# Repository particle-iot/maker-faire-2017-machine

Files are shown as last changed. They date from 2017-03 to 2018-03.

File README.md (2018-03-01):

# Maker Faire Machine

Welcome friends! Put all the amazing code, diagrams, PCB files and other
artifacts needed to build the Machine here.

# License

Copyright (C) 2017 Particle Industries Inc
All software code is licensed under the MIT license
All hardware designs are licensed under the Creative Commons Attribution-ShareAlike (CC-BY-SA) license

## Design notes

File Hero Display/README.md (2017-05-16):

This is the animation that runs on a monitor powered by a Raspberry Pi.

It gets information about the machine from Particle firmware running on the same Pi.

### Running

Start a web server here and view http://localhost:8080/index.html

```
ruby -run -e httpd -- Website
```

### References

- Animating SVG https://davidwalsh.name/svg-animations-snap
- Snap.svg library docs http://snapsvg.io/docs/
- Snap.svg examples http://snapsvg.io/demos/
- Snap.svg snippets http://svg.dabbles.info/

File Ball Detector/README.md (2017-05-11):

# Ball Detector

## Parts

- Bracket (designed with Fusion 360) http://a360.co/2oVDeuF
- Round bracket with laser in the middle (designed with Fusion 360) http://a360.co/2qUFsPa		
- Round bracket with laser offset (designed with Fusion 360) http://a360.co/2q6rvfz
- Laser Diode https://www.amazon.com/gp/product/B01ITK4PEO
- Photoresistor https://www.amazon.com/gp/product/B016D737Y4

## Circuit

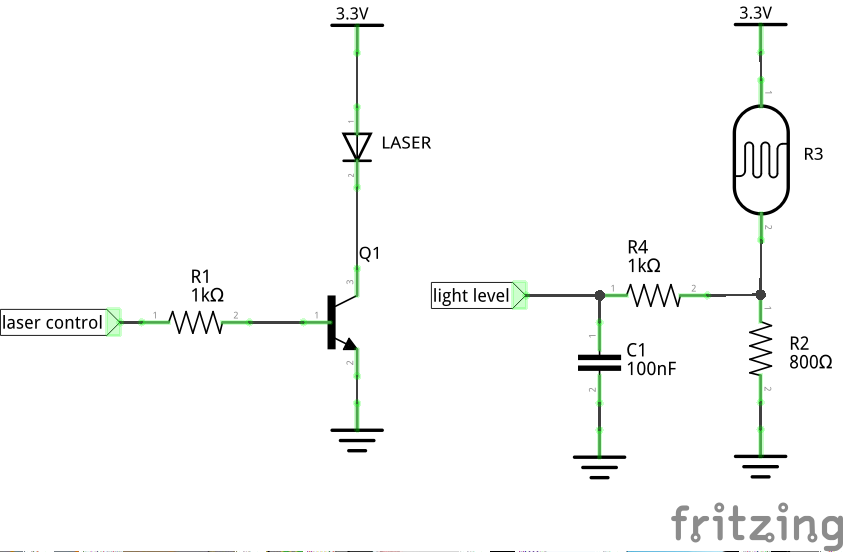
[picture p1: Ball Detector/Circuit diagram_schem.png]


Open points / suggestions:
- Use a potentiometer instead of a fixed pull down resistor for the photoresistor to allow calibrating the edges on site. 2 kOhm potentiometer suggested.
- Add a low-pass RC filter to the light level pin to filter out high frequency noise.

## Software Library

https://github.com/spark/library-beam-detector

## Assembly

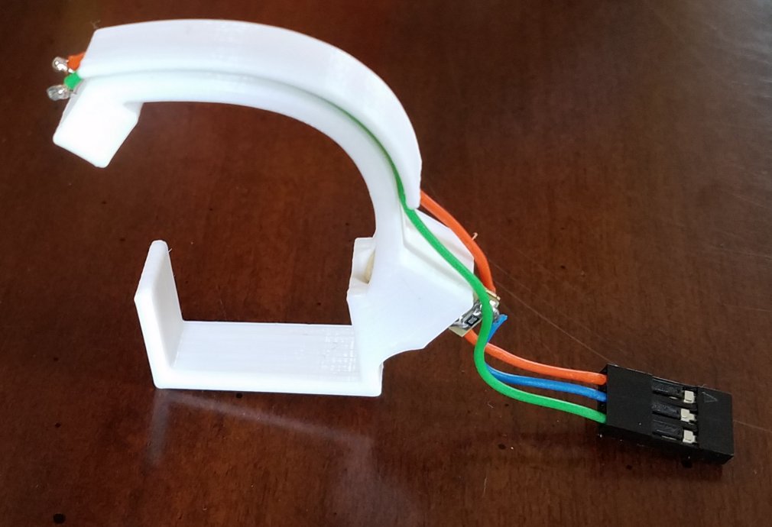
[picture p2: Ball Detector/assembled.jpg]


- 3d print the bracket. I used 0.2 mm layer height, 5% rectilinear infill.
- Insert the laser diode loosely. If the laser diode is too loose or doesn't fit in the hole,
  tweak the diameter in Fusion 360 and print again. If it is a tad too
  tight, manually turn a 15/64" drill bit in the hole to remove some of
  the imperfections from the print.
- Insert the photoresistor. I like cutting one leg shorter than the
other so I can insert them one at at time in the tiny holes.
- Connect a multimeter to the photoresistor in resistance measurement mode.
- Connect a power supply (3.3V or 5V) to the laser diode. Blue is ground, red is positive.
- Rotate the laser diode in the hole to get the smallest resistance measurement on the photoresistor.
- Press the laser diode firmly in.
- Solder some wires to the photoresistor wires and shove the wires inside the channel.
- Unsolder the laser diode wires and solder some sturdier wires.

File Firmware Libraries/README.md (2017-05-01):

Some firmware libraries to use in the Maker Faire Machine modules.

## Simple Storage

For loading and storing parameters in the EEPROM. See the file `examples/basic/basic.ino`

For each panel, use app code with the panel number, i.e. `APP_CODE('M', 'F', 0, 2)` for second panel.

## Communication

For sharing state between multiple modules through the CAN bus.

## Beam Detector

Ball detector using a laser break beam

## HSV

Convert between red/green/blue colors and hue/saturation/value colors.

## Encoder

Count pulses from a quadrature rotary encoder.

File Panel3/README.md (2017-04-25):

# Panel 3

**Sensor:** Rotary encoder (quadrature)
**Mechanism:** ball lifter with multiple paths/runs
**Story:** Particle cloud routes and delivers the data internally

[See spreadsheet](https://docs.google.com/spreadsheets/d/1myQVK4iyX1niJGtPiAOqu2GMmV2cjAntq5kpxnjmFF0/edit#gid=340408367)
for more info.

## TOC

* Mechanical drawings
* BOM
* PCB
* Firmware
* Tweakable parameters

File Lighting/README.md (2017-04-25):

# Lighting

This is the module that powers the lights behind the interaction surface.

When nobody is interacting with the panels, the lights show a white pattern.

The lights change to a colorful pattern when people interact with each panel.

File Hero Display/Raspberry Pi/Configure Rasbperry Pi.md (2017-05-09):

## Raspberry Pi for running the Hero Display

### Prepare OS

Download the latest Raspbian and write the image to the SD card.

Eject the SD card and reinsert it. You should now see a partition called boot.

Add a file called `wpa_supplicant.conf` with your network info on the
boot partition.
```
network={
   ssid="my_ssid"
   psk="supersekrit"
   key_mgmt=WPA-PSK
}
```

Insert the SD card to the Raspberry Pi and apply power.

After a minute you should be able to `ping raspberrypi.local`

Copy you SSH key to the Pi `ssh-copy-id pi@raspberrypi.local`

Log in to the Pi remotely `ssh pi@raspberrypi.local`

Edit `/boot/cmdline.txt` and add `usbhid.mousepoll=0` to fix the laggy mouse in the GUI.

Run `sudo raspi-config`

- Change the password to the same password as the Maker Faire 2017 Particle user.
- Change the hostname to `hero`

Exit raspi-config and reboot.

### Enable CAN driver

Edit `/boot/config.txt` and add these lines at the end

```
# Load CAN driver
dtparam=spi=on
dtoverlay=mcp2515-can0-overlay,oscillator=16000000,interrupt=25
dtoverlay=spi-bcm2835-overlay
```

Install CAN utils `sudo apt install can-utils`

CAN utils are user applications that use the Linux socketcan interface
to send, receive and dump CAN message.

### Set static IP on network card

```
sudo vim /etc/dhcpcd.conf
```

Paste at the end:
```
interface eth0
static ip_address=192.168.1.1/24
```

### Install particle-agent

```
bash <( curl -sL https://particle.io/install-pi )
```

Log in with software+mf2017@particle.io

Call the device `hero`

### Setup web server

```
sudo apt install nginx
```

Edit `/etc/nginx/sites-available/default` to:
```
root /home/pi/website
```

```
sudo service nginx restart
```

### Flash firmware

```
make compile
# outputs firmware.bin
```

Copy firmware to Pi
```
scp firmware.bin pi@hero.lan:
```

Replace firmware (local OTA...)
```
ssh pi@hero.lan
sudo cp firmware.bin /var/lib/particle/devices/7ab72efbc4b6719da784073f/output.bin
particle-agent restart
```

### Start browser on boot

Set the browser home page to http://localhost

Install mouse cursor hiding package
```
sudo apt install unclutter
```

Edit `~/.config/lxsession/LXDE-pi/autostart`

Add
```
#Disable screensaver:
@xset s noblank
@xset s off
@xset -dpms
#Start browser on boot
@chromium-browser --app=http://localhost --start-fullscreen
#Hide mouse pointer
@unclutter -idle 1 -root
```

### Download animation

Generate an ssh key on the Pi
```
ssh-keygen
```

Add the `~/.ssh/id_rsa.pub` to the [Maker Faire Machine repo](https://github.com/spark/maker-faire-2017-machine/settings/keys) with read/write permissions.

Clone the repo to the Pi
```
git clone git@github.com:spark/maker-faire-2017-machine.git
```

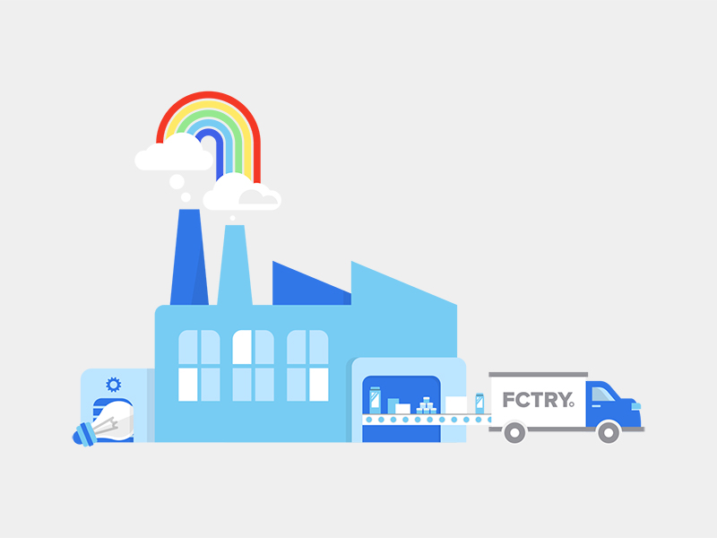
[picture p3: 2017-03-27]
Hero Display/Graphics/fctry-concept.jpg

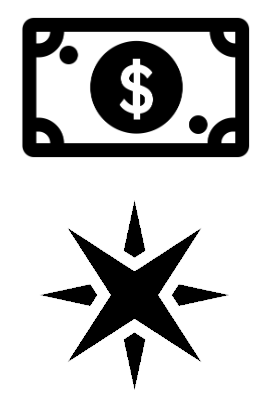
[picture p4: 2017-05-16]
Panel4/firmware/images/p_money.bmp

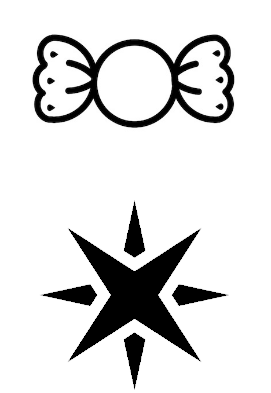
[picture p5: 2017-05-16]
Panel4/firmware/images/p_candy.bmp

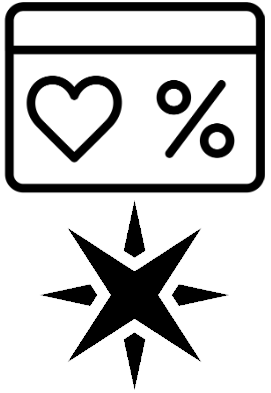
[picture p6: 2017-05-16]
Panel4/firmware/images/p_coupon.bmp

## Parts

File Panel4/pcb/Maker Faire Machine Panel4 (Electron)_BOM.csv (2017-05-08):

Qty-1 | Part References | Value | Package | Mfg Part Num | Mfg Name | VID | Vendor Part Num | Description | XREF
0 | JP2(DNP) |  | 1X03_NO_SILK | ***PART# '*' NOT FOUND*** | * | * | * | * | *
1 | JP1 |  | 2X10_MOLEX_MX150 | 348302001 | Molex | DK | WM12752-ND | MX150 RA HDR 2X10 ST BLK KEY A | REF77
1 | D1 |  | SMA-DIODE | B230A-13-F | Diodes-Incorporated | DK | B230A-FDICT-ND | DIODE SCHOTTKY 30V 2A SMA | REF43
1 | Q1 |  | TO-92-AMMO | PN2222ABU | Fairchild Semiconductor | DK | PN2222AFS-ND | TRANSISTOR NPN TO92 | REF75
2 | C3, C5 | 0.1uF | 1206 | 12065C104KAT2A | AVX | DK | 478-1556-1-ND | CERAMIC CAPACITOR 0.1UF 50V X7R 10% 1206 | REF61
3 | C1, C2, C6 | 0.01uF | 1206 | 12065C103KAT2A | AVX | DK | 478-1542-1-ND | MLCC CAPACITOR 0.01uF 50V X7R 10% 1206 FULL REEL | REF62
4 | R1, R2, R3, R4 | 1k | 1206 | ERJ-8ENF1001V | Panasonic | DK | P1.00KFCT-ND | RES SMD 1K OHM 1% 1/4W 1206 | REF74
3 | RV1, RV2, RV3 | 2k | 3362U | 3362U-1-202LF | Bourns Inc. | DK | 3362U-202LF-ND | TRIMMER 2K OHM 0.5W PC PIN | REF72
1 | C4 | 100uF | CPOL-RADIAL-100UF-25V | EEU-FM1H101B | Panasonic Electronic Components | DK | P19712CT-ND | CAP ALUM 100UF 20% 50V RADIAL | REF76
50 | CONN_TERM | BOM-ENTRY | * | 330122002 | Molex | DK | WM3687CT-ND | TERM RCPT TIN 18-20AWG SLD | REF79
1 | CONN_HOUSING | BOM-ENTRY | * | 334722001 | Molex | DK | WM4737-ND | CONN RCPT 20POS DUAL BLACK | REF78
1 | ELECTRON | ELECTRON_WITH_STACKABLE_HEADERS | ELECTRON_STACKABLE | ***PART# '*' NOT FOUND*** | * | * | * | * | *
1 | IC1 | TJA1049 | SO8 | TJA1049T-118 | NXP Semiconductors | DK | 568-8682-1-ND | IC CAN TRANSEIVER HS 8SOIC | REF16

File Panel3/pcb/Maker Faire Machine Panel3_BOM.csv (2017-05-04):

Qty-1 | Part References | Value | Package | Mfg Part Num | Mfg Name | VID | Vendor Part Num | Description | XREF
1 | D1 |  | SMA-DIODE | B230A-13-F | Diodes-Incorporated | DK | B230A-FDICT-ND | DIODE SCHOTTKY 30V 2A SMA | REF43
4 | JP3, JP6, JP8, JP9 |  | SCREWTERMINAL-3.5MM-2 | OSTTE020104 | On Shore Technology Inc. | DK | ED2740-ND | TERMINAL BLOCK 3.5MM 2POS PCB | REF68
2 | JP10, JP5 |  | SCREWTERMINAL-3.5MM-4 | OSTTE030104 | On Shore Technology Inc. | DK | ED2741-ND | TERMINAL BLOCK 3.5MM 3POS PCB | REF69
3 | JP1, JP2, JP4 |  | SCREWTERMINAL-3.5MM-4 | OSTTE040104 | On Shore Technology Inc. | DK | ED2742-ND | TERMINAL BLOCK 3.5MM 4POS PCB | REF70
2 | Q1, Q2 |  | TO-92 | PN2222ABU | Fairchild Semiconductor | DK | PN2222AFS-ND | TRANSISTOR NPN TO92 | REF75
1 | D2 |  | LED5MM | SSL-LX5093HD | Lumex | DK | 67-1102-ND | LED RED DIFF 5MM ROUND T/H | REF73
2 | C3, C5 | 0.1uF | 1206 | 12065C104KAT2A | AVX | DK | 478-1556-1-ND | CERAMIC CAPACITOR 0.1UF 50V X7R 10% 1206 | REF61
2 | C1, C2 | 0.01uF | 1206 | 12065C103KAT2A | AVX | DK | 478-1542-1-ND | MLCC CAPACITOR 0.01uF 50V X7R 10% 1206 FULL REEL | REF62
5 | R1, R2, R3, R4, R6 | 1k | 1206 | ERJ-8ENF1001V | Panasonic | DK | P1.00KFCT-ND | RES SMD 1K OHM 1% 1/4W 1206 | REF74
2 | RV1, RV2 | 2k | 3362U | 3362U-1-202LF | Bourns Inc. | DK | 3362U-202LF-ND | TRIMMER 2K OHM 0.5W PC PIN | REF72
1 | C4 | 100uF | CPOL-RADIAL-100UF-25V | EEU-FM1H101B | Panasonic Electronic Components | DK | P19712CT-ND | CAP ALUM 100UF 20% 50V RADIAL | REF76
1 | U$1 | PHOTON_SMD | PHOTON_SMD | ***PART# '*' NOT FOUND*** | * | * | * | * | *
1 | JP7 | POWER_JACKSLT | POWER_JACK_SLOT | PJ-202A | CUI Inc. | DK | CP-202A-ND | CONN PWR JACK 2X5.5MM KINKED PIN | REF71
1 | IC1 | TJA1049 | SO8 | TJA1049T-118 | NXP Semiconductors | DK | 568-8682-1-ND | IC CAN TRANSEIVER HS 8SOIC | REF16

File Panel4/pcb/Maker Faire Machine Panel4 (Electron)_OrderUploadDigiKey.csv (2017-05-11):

Digi-Key Part No. | Manufacturer Name | Mfr Part No. | Customer Reference | Qty1
* | * | * | ELECTRON/JP2 | 1 | *** PART# '*' NOT FOUND : ELECTRON/JP2
3362U-202LF-ND | Bourns Inc. | 3362U-1-202LF | RV1/RV2/RV3 | 3
478-1542-1-ND | AVX | 12065C103KAT2A | C1/C2/C6 | 3
478-1556-1-ND | AVX | 12065C104KAT2A | C3/C5 | 2
WM3687CT-ND | Molex | 330122002 | CONN_TERM | 1
WM4737-ND | Molex | 334722001 | CONN_HOUSING | 1
WM12752-ND | Molex | 348302001 | JP1 | 1
B230A-FDICT-ND | Diodes-Incorporated | B230A-13-F | D1 | 1
P19712CT-ND | Panasonic Electronic Components | EEU-FM1H101B | C4 | 1
P1.00KFCT-ND | Panasonic | ERJ-8ENF1001V | R1/R2/R3/R4 | 4
PN2222AFS-ND | Fairchild Semiconductor | PN2222ABU | Q1 | 1
568-8682-1-ND | NXP Semiconductors | TJA1049T-118 | IC1 | 1

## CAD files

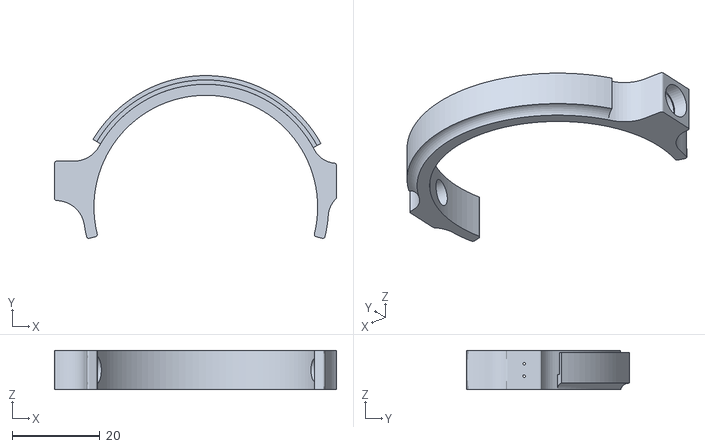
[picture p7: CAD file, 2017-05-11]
Ball Detector/Round ball detector B.stl
64.3 x 37.1 x 9.00

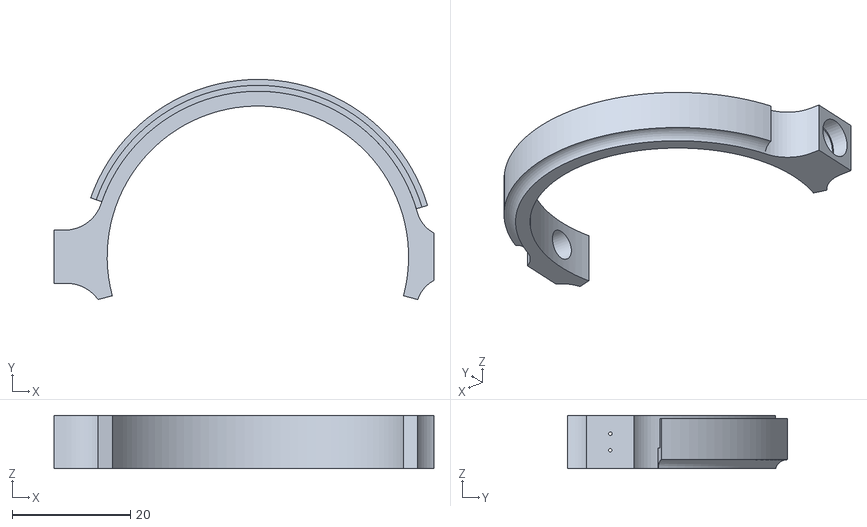
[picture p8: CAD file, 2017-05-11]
Ball Detector/Round ball detector A.stl
64.3 x 37.2 x 9.00

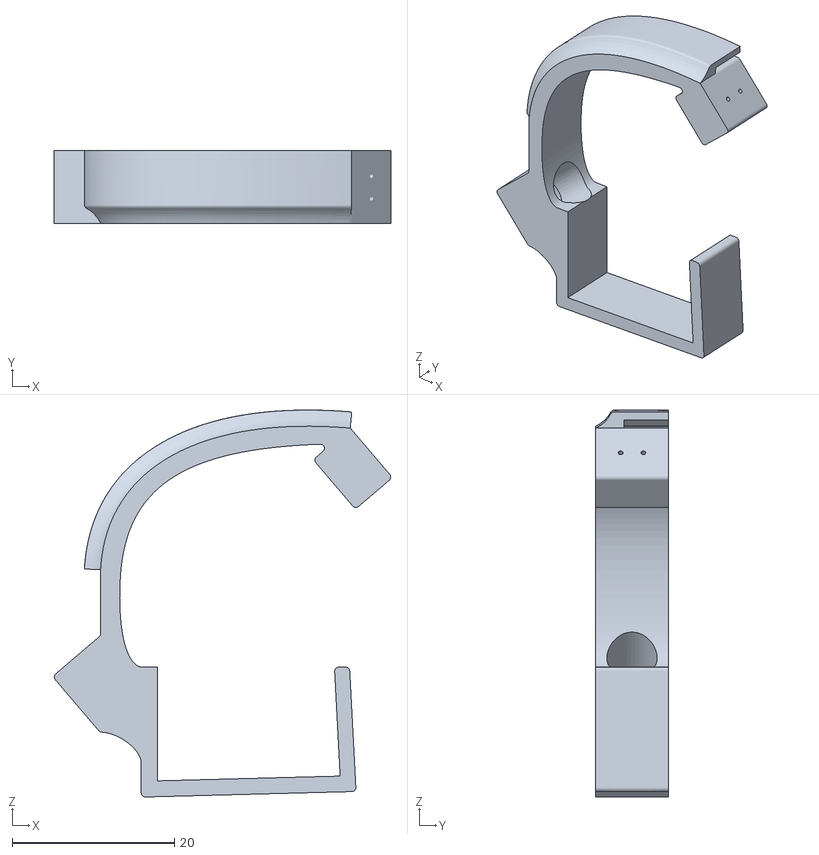
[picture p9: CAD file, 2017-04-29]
Ball Detector/Ball Detector F.stl
41.5 x 9.00 x 47.7

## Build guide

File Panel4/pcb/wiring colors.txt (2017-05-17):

can bus
 1 CANL green
 2 CANH yellow

 3 S2 white - stepper direction?
 4 S3 white - unused

laser ground and / laser vcc
 5 LG black
 6 LV orange

vcc for laser gates
 7 3.3V orange

laser gates
 8 SIG1 blue - A1
 9 SIG2 green - A2
10 SIG3 yellow - A3

POWER IN
11 5V orange
12 GND black

13 S1 white - stepper enable
14 STEP white - stepper step / pwm

HOVER
15 3.3V orange
16 GND black
17 HRST blue
18 HTS white
19 SCL green
20 SDA yellow

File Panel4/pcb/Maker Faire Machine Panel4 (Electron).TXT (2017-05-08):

%
M48
M72
T01C0.02362
T02C0.02756
T03C0.03200
T04C0.04000
T05C0.05906
T06C0.13000
T07C0.15748
%
T01
X11800Y34300
X11800Y51800
X11800Y71800
X11800Y91800
X11800Y109300
X11800Y126800
X36800Y136800
X11800Y166800
X39300Y199300
X14300Y209300
X36800Y244300
X84300Y184300
X94300Y184300
X116800Y156800
X126800Y156800
X126800Y134300
X159300Y159300
X149300Y189300
X138050Y189300
X166800Y200550
X191800Y166800
X191800Y154300
X209300Y166800
X219300Y209300
X191800Y241800
X119300Y244300
X76800Y136800
X81800Y79300
X70550Y79300
X106800Y79300
X131800Y78050
X141800Y78050
X124300Y11800
X204300Y78050
X221800Y71800
X221800Y54300
X221800Y34300
X221800Y89300
X221800Y106800
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

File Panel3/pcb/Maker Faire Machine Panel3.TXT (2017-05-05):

%
M48
M72
T01C0.02362
T02C0.02756
T03C0.03200
T04C0.03937
T05C0.04000
T06C0.04724
T07C0.13000
%
T01
X126800Y116800
X136800Y116800
X191800Y91800
X261800Y106800
X291800Y86800
X276800Y61800
X321800Y101800
X321800Y131800
X286800Y166800
X301800Y171800
X286800Y181800
X276800Y191800
X271800Y186800
X261800Y166800
X276800Y141800
X241800Y216800
X341800Y241800
X126800Y226800
T02
X141800Y196800
X151800Y196800
T03
X261800Y211800
X261800Y221800
X261800Y231800
X101800Y326800
X91800Y326800
X81800Y326800
X81800Y41800
X91800Y41800
T04
X161643Y292469
X141957Y304280
X161643Y317272
T05
X196800Y321800
X196800Y311800
X196800Y301800
X196800Y291800
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

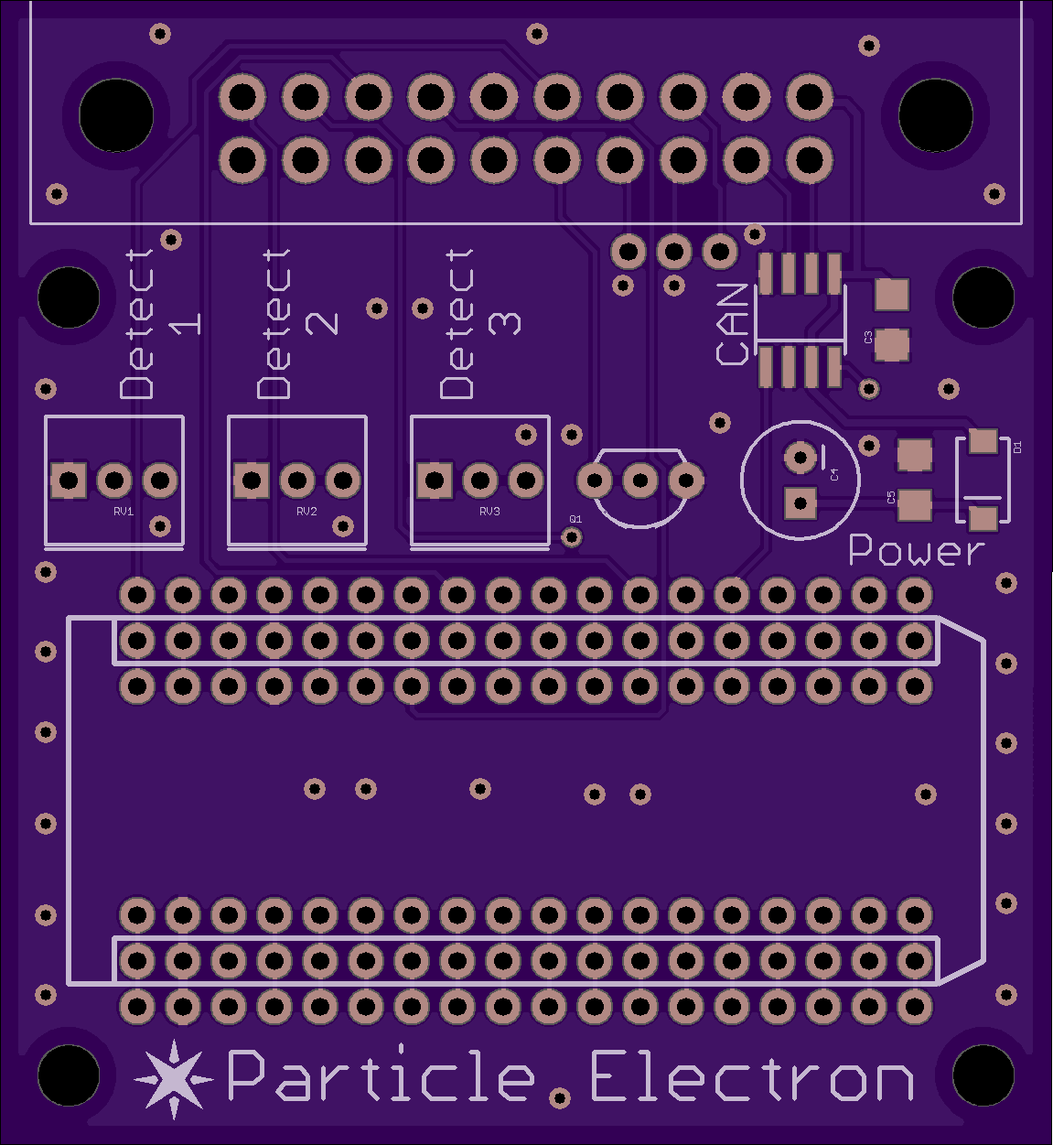
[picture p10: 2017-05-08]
Panel4/pcb/Maker Faire Machine Panel4 (Electron) Top.png

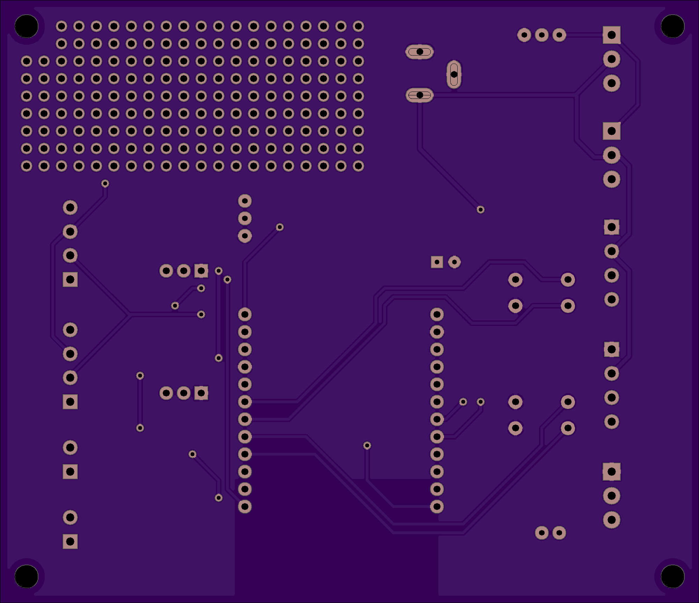
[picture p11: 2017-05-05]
Panel3/pcb/Maker Faire Machine Panel3 PCB Bottom.png

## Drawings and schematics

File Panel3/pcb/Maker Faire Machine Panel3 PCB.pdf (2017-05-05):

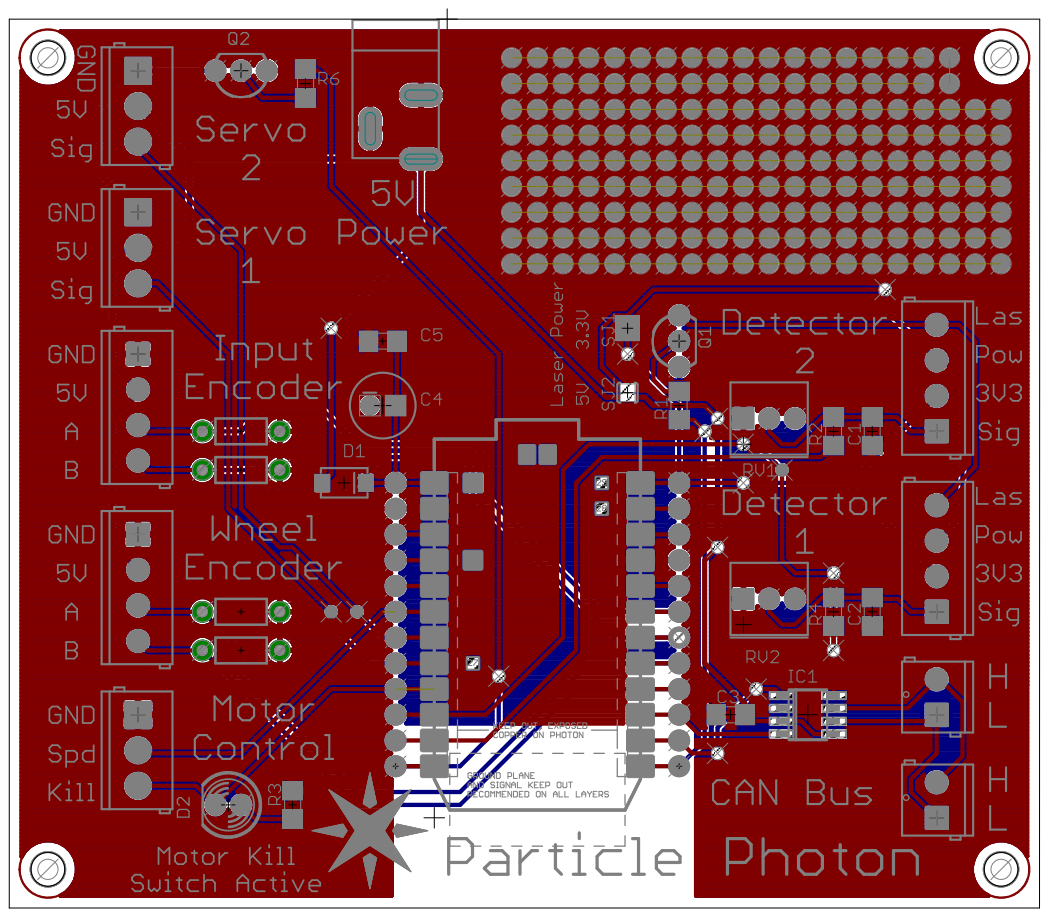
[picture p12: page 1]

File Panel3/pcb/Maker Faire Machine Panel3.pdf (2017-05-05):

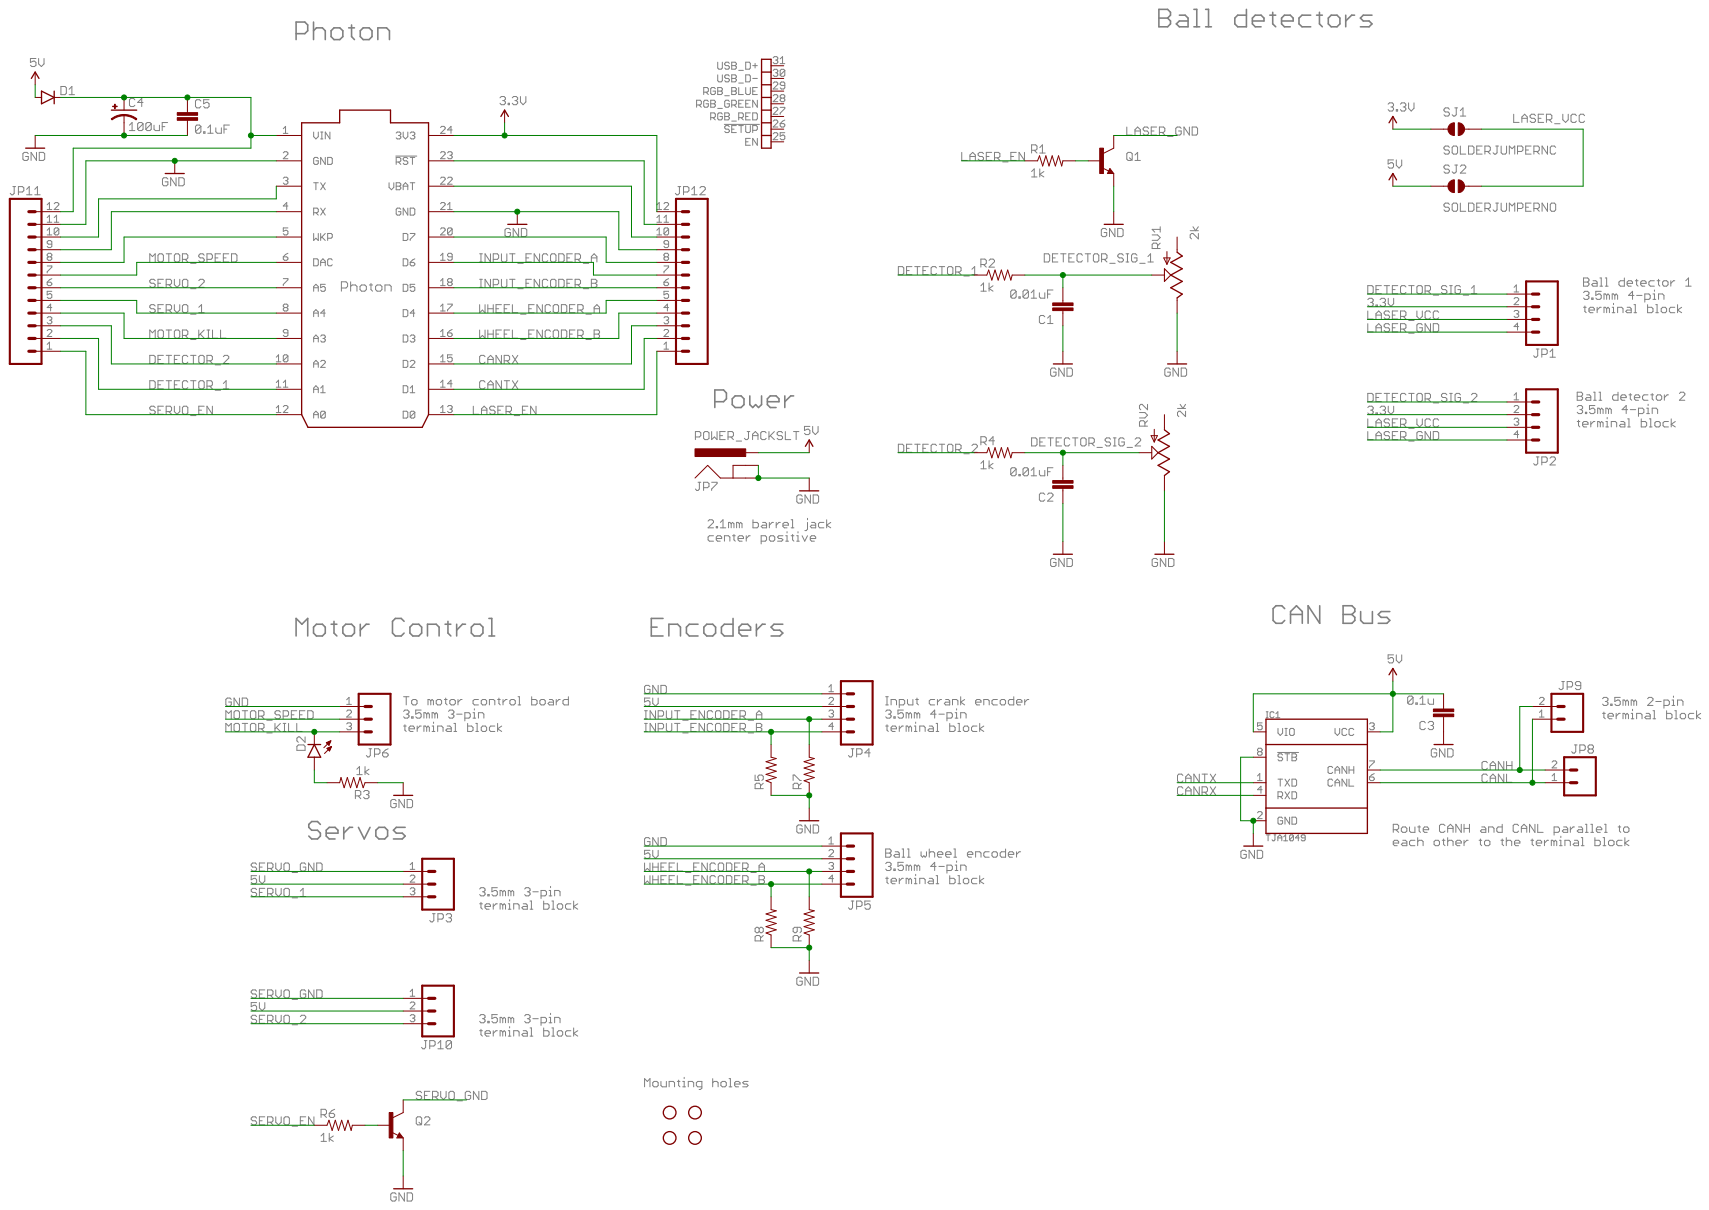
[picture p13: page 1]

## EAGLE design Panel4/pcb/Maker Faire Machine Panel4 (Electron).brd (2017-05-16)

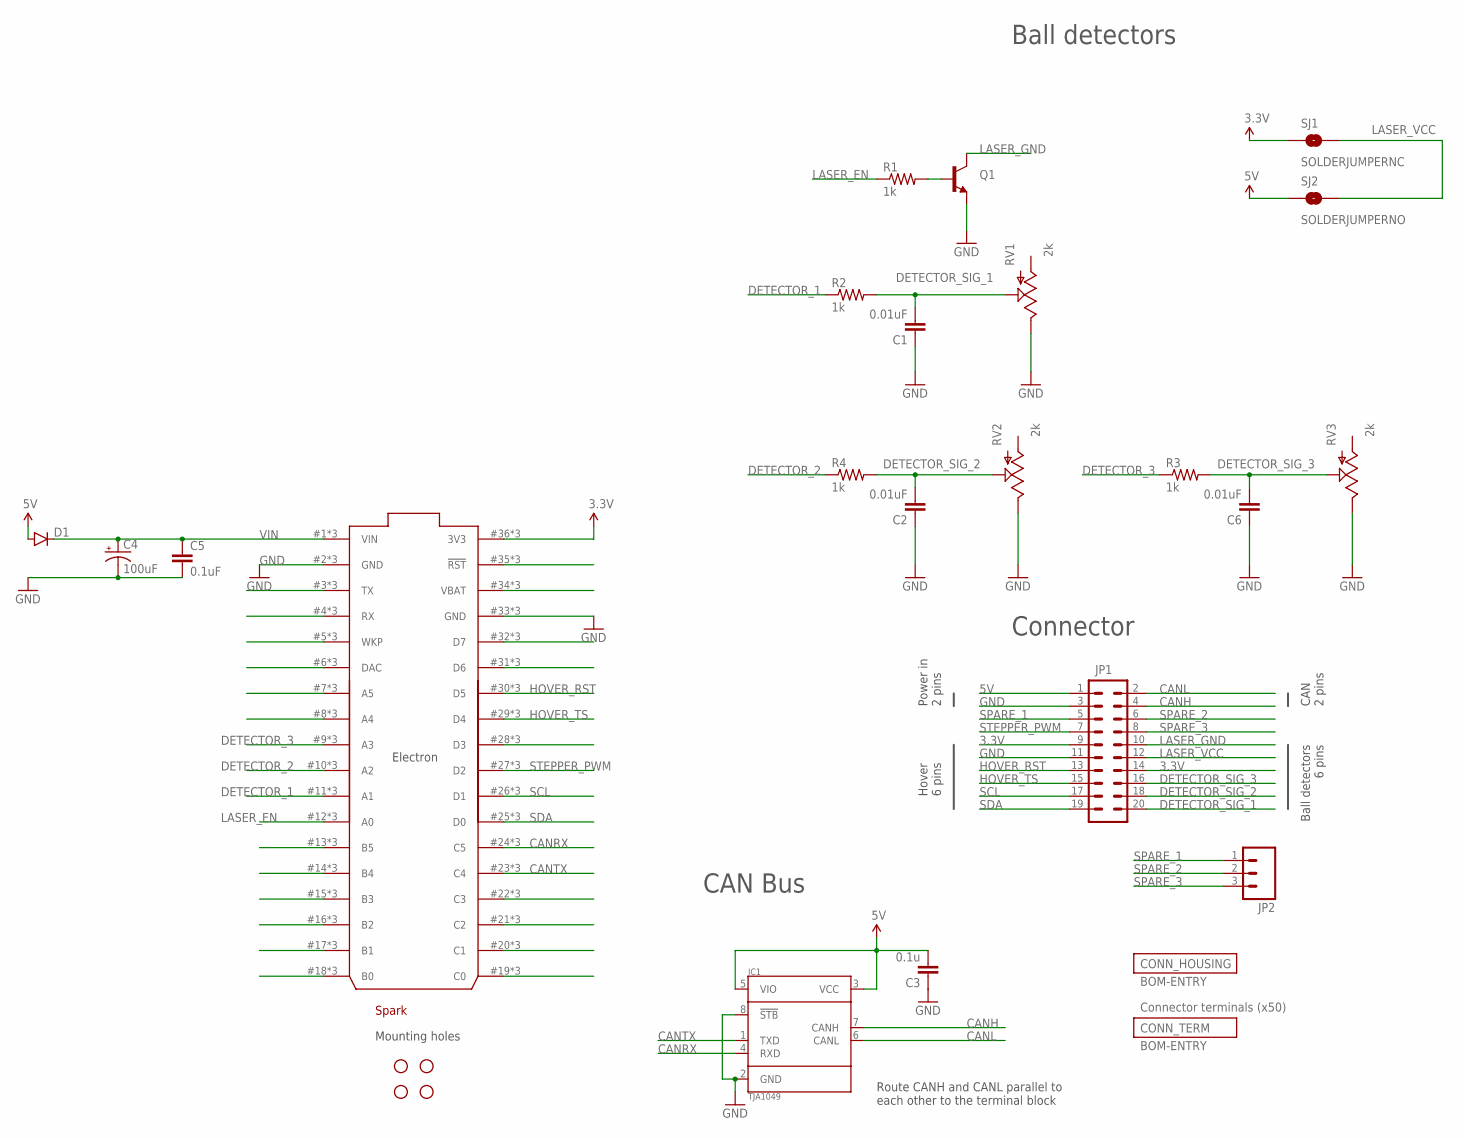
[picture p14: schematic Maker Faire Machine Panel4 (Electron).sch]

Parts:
C1, C2, C6: 0.01uF; 1206; PARTNO 12065C103KAT2A
C3: 0.1u; 1206; PARTNO 12065C104KAT2A
C4: 100uF; CPOL-RADIAL-100UF-25V; PARTNO EEU-FM1H101B
C5: 0.1uF; 1206; PARTNO 12065C104KAT2A
D1: DIODESMA; SMA-DIODE; PARTNO B230A-13-F
ELECTRON: ELECTRON_WITH_STACKABLE_HEADERS; ELECTRON_STACKABLE
IC1: TJA1049; SO8; PARTNO TJA1049T-118
JP1: M10X2_MMOLEX_MX150; 2X10_MOLEX_MX150; PARTNO 348302001
JP2: M031X03_NO_SILK; 1X03_NO_SILK
Q1: TRANSISTOR_NPNTO-92-AMMO; TO-92-AMMO; PARTNO PN2222ABU
R1, R2, R3, R4: 1k; 1206; PARTNO ERJ-8ENF1001V
RV1, RV2, RV3: 2k; 3362U; PARTNO 3362U-1-202LF
SJ1: SOLDERJUMPERNC; SJ_2S
SJ2: SOLDERJUMPERNO; SJ_2S-NO
STANDOFF1, STANDOFF2, STANDOFF3, STANDOFF4: STAND-OFF
U$2: SPARK_LOGOSILK; SPARK_LOGO_SILK

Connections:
3.3V: ELECTRON.36 (3V3), ELECTRON.#36 (3V3), ELECTRON.@36 (3V3), JP1.9, JP1.14, SJ1.1
5V: C3.2, D1.A, IC1.3 (VCC), IC1.5 (VIO), JP1.1, SJ2.1
CANH: IC1.7 (CANH), JP1.4
CANL: IC1.6 (CANL), JP1.2
CANRX: ELECTRON.24 (C5), ELECTRON.#24 (C5), ELECTRON.@24 (C5), IC1.4 (RXD)
CANTX: ELECTRON.23 (C4), ELECTRON.#23 (C4), ELECTRON.@23 (C4), IC1.1 (TXD)
DETECTOR_1: ELECTRON.11 (A1), ELECTRON.#11 (A1), ELECTRON.@11 (A1), R2.1
DETECTOR_2: ELECTRON.10 (A2), ELECTRON.#10 (A2), ELECTRON.@10 (A2), R4.1
DETECTOR_3: ELECTRON.9 (A3), ELECTRON.#9 (A3), ELECTRON.@9 (A3), R3.1
DETECTOR_SIG_1: C1.2, JP1.20, R2.2, RV1.P$2 (S)
DETECTOR_SIG_2: C2.2, JP1.18, R4.2, RV2.P$2 (S)
DETECTOR_SIG_3: C6.2, JP1.16, R3.2, RV3.P$2 (S)
GND: C1.1, C2.1, C3.1, C4.2 (-), C5.2, C6.1, ELECTRON.2 (GND), ELECTRON.33 (GND), ELECTRON.#2 (GND), ELECTRON.#33 (GND), ELECTRON.@2 (GND), ELECTRON.@33 (GND), IC1.2 (GND), IC1.8 (!STB), JP1.3, JP1.11, Q1.1 (E), RV1.P$1 (E), RV2.P$1 (E), RV3.P$1 (E)
HOVER_RST: ELECTRON.30 (D5), ELECTRON.#30 (D5), ELECTRON.@30 (D5), JP1.13
HOVER_TS: ELECTRON.29 (D4), ELECTRON.#29 (D4), ELECTRON.@29 (D4), JP1.15
LASER_EN: ELECTRON.12 (A0), ELECTRON.#12 (A0), ELECTRON.@12 (A0), R1.1
LASER_GND: JP1.10, Q1.3 (C)
LASER_VCC: JP1.12, SJ1.2, SJ2.2
unnamed: ELECTRON.35 (!RST), ELECTRON.#35 (!RST), ELECTRON.@35 (!RST)
unnamed: ELECTRON.34 (VBAT), ELECTRON.#34 (VBAT), ELECTRON.@34 (VBAT)
unnamed: Q1.2 (B), R1.2
unnamed: ELECTRON.32 (D7), ELECTRON.#32 (D7), ELECTRON.@32 (D7)
unnamed: ELECTRON.31 (D6), ELECTRON.#31 (D6), ELECTRON.@31 (D6)
unnamed: ELECTRON.28 (D3), ELECTRON.#28 (D3), ELECTRON.@28 (D3)
unnamed: ELECTRON.8 (A4), ELECTRON.#8 (A4), ELECTRON.@8 (A4)
unnamed: ELECTRON.7 (A5), ELECTRON.#7 (A5), ELECTRON.@7 (A5)
unnamed: ELECTRON.6 (DAC), ELECTRON.#6 (DAC), ELECTRON.@6 (DAC)
unnamed: ELECTRON.5 (WKP), ELECTRON.#5 (WKP), ELECTRON.@5 (WKP)
unnamed: ELECTRON.4 (RX), ELECTRON.#4 (RX), ELECTRON.@4 (RX)
unnamed: ELECTRON.3 (TX), ELECTRON.#3 (TX), ELECTRON.@3 (TX)
unnamed: ELECTRON.22 (C3), ELECTRON.#22 (C3), ELECTRON.@22 (C3)
unnamed: ELECTRON.21 (C2), ELECTRON.#21 (C2), ELECTRON.@21 (C2)
unnamed: ELECTRON.20 (C1), ELECTRON.#20 (C1), ELECTRON.@20 (C1)
unnamed: ELECTRON.19 (C0), ELECTRON.#19 (C0), ELECTRON.@19 (C0)
unnamed: ELECTRON.18 (B0), ELECTRON.#18 (B0), ELECTRON.@18 (B0)
unnamed: ELECTRON.17 (B1), ELECTRON.#17 (B1), ELECTRON.@17 (B1)
unnamed: ELECTRON.16 (B2), ELECTRON.#16 (B2), ELECTRON.@16 (B2)
unnamed: ELECTRON.15 (B3), ELECTRON.#15 (B3), ELECTRON.@15 (B3)
unnamed: ELECTRON.14 (B4), ELECTRON.#14 (B4), ELECTRON.@14 (B4)
unnamed: ELECTRON.13 (B5), ELECTRON.#13 (B5), ELECTRON.@13 (B5)
SCL: ELECTRON.26 (D1), ELECTRON.#26 (D1), ELECTRON.@26 (D1), JP1.17
SDA: ELECTRON.25 (D0), ELECTRON.#25 (D0), ELECTRON.@25 (D0), JP1.19
SPARE_1: JP1.5, JP2.1
SPARE_2: JP1.6, JP2.2
SPARE_3: JP1.8, JP2.3
STEPPER_PWM: ELECTRON.27 (D2), ELECTRON.#27 (D2), ELECTRON.@27 (D2), JP1.7
VIN: C4.1 (+), C5.1, D1.C, ELECTRON.1 (VIN), ELECTRON.#1 (VIN), ELECTRON.@1 (VIN)

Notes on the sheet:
Route CANH and CANL parallel to each other to the terminal block
Ball detectors
Hover 6 pins
CAN 2 pins
Ball detectors 6 pins
Connector
CAN Bus
Mounting holes
Power in 2 pins

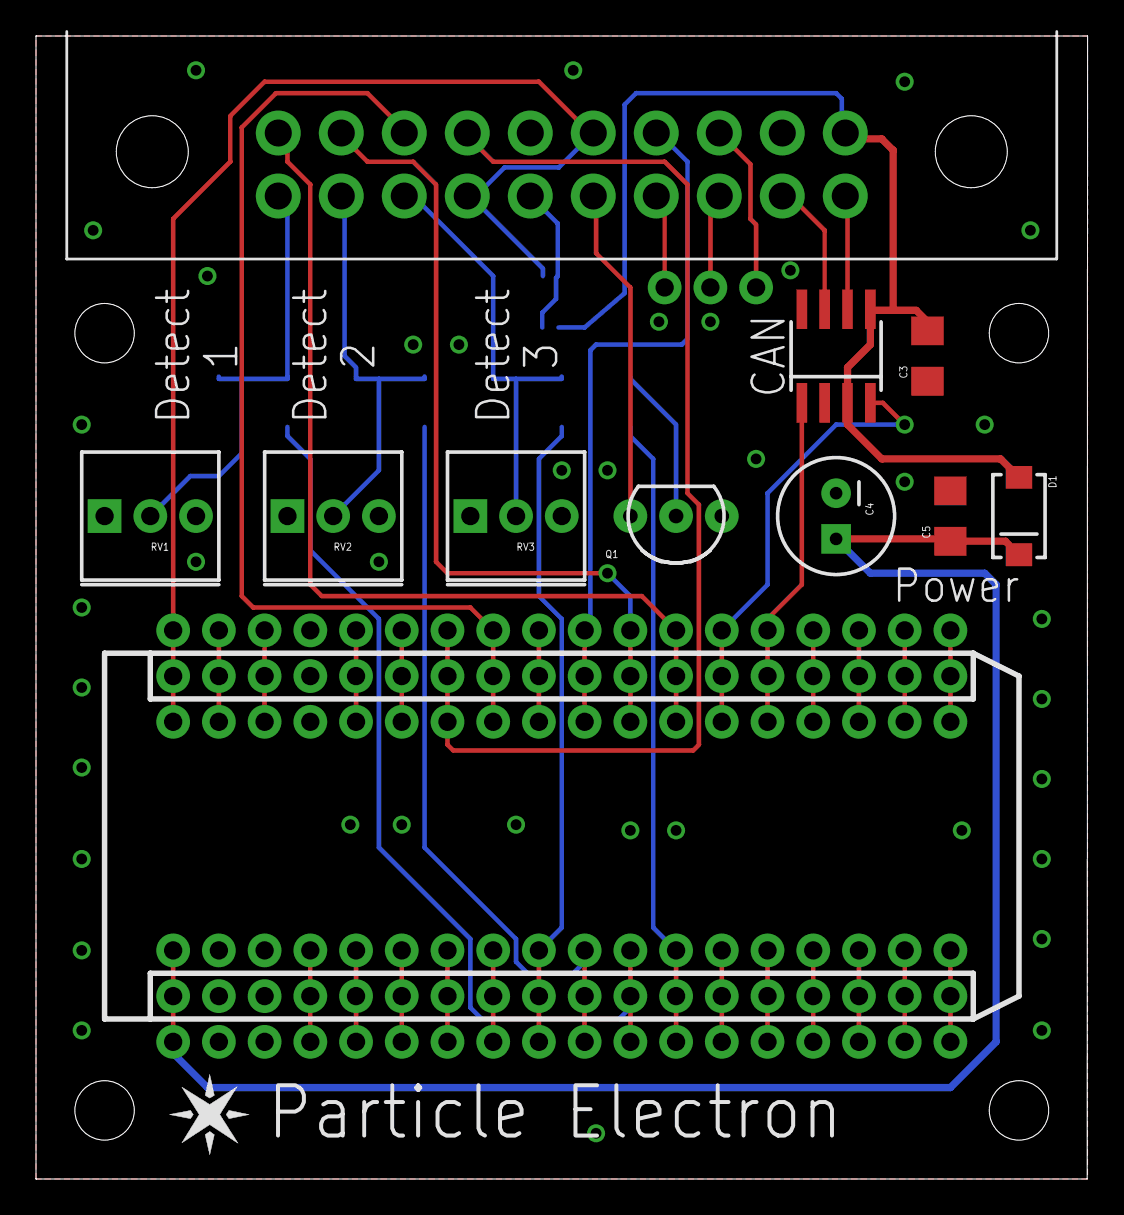
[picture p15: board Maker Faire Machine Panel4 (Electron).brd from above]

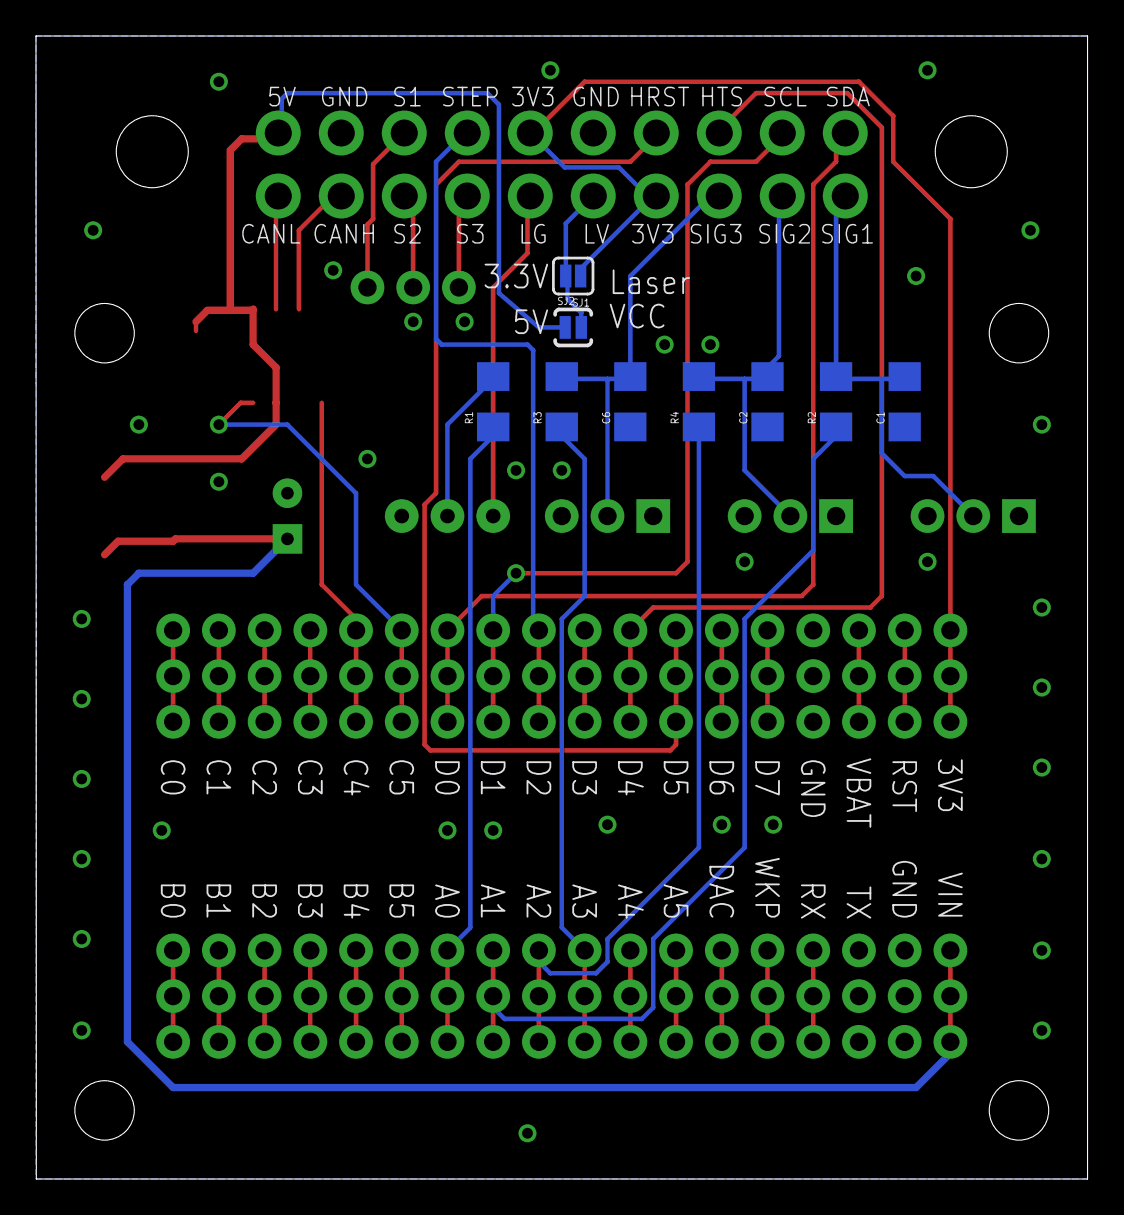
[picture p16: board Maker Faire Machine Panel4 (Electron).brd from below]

Board: 2 copper layers, 58.4 x 63.5 mm, 26 parts (9 on the bottom side), 47 nets.

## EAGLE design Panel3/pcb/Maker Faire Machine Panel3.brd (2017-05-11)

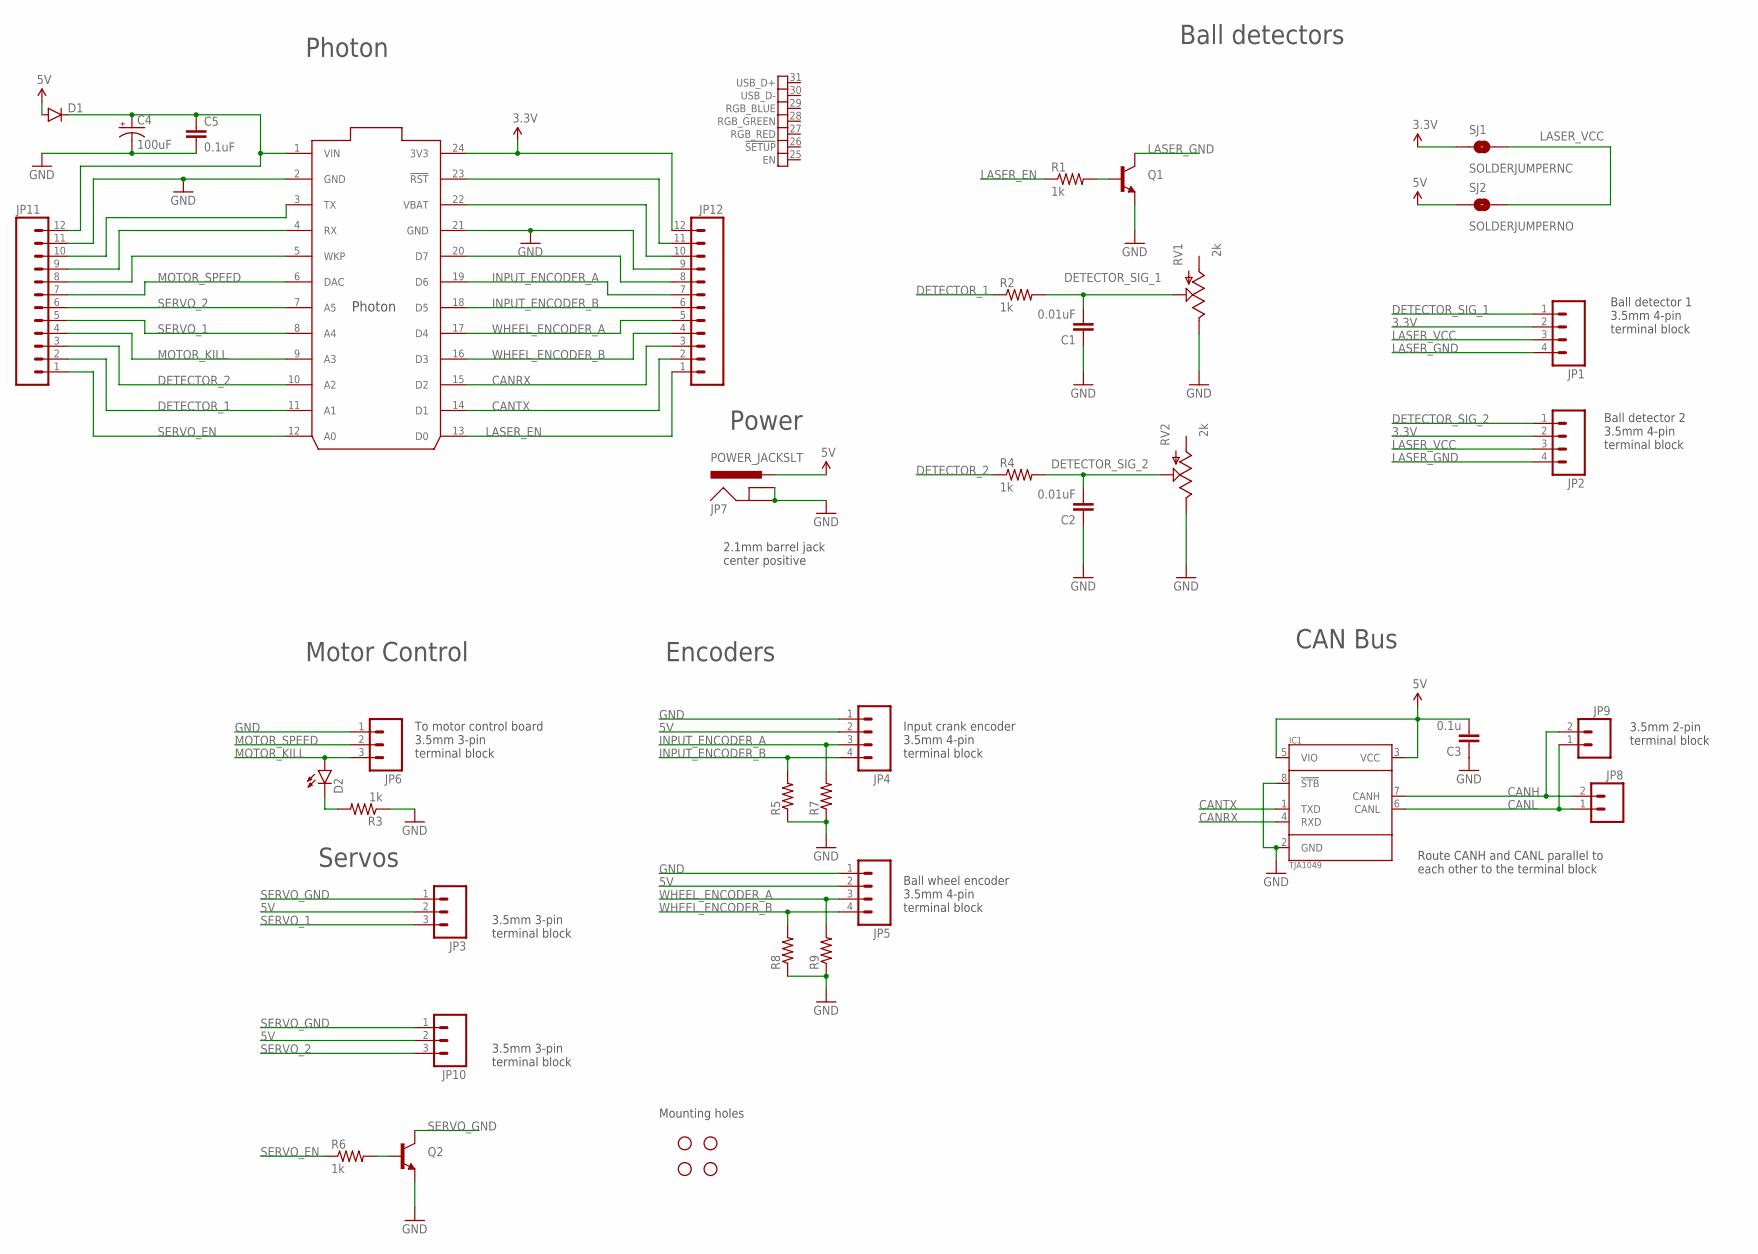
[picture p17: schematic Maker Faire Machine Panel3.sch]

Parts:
C1, C2: 0.01uF; 1206; PARTNO 12065C103KAT2A
C3: 0.1u; 1206; PARTNO 12065C104KAT2A
C4: 100uF; CPOL-RADIAL-100UF-25V; PARTNO EEU-FM1H101B
C5: 0.1uF; 1206; PARTNO 12065C104KAT2A
D1: DIODESMA; SMA-DIODE; PARTNO B230A-13-F
D2: LED5MM; PARTNO SSL-LX5093HD
IC1: TJA1049; SO8; PARTNO TJA1049T-118
JP1, JP2, JP4: M04SCREW; SCREWTERMINAL-3.5MM-4; PARTNO OSTTE040104
JP3, JP6: M03SCREW; SCREWTERMINAL-3.5MM-3; PARTNO OSTTE020104
JP5: M04SCREW; SCREWTERMINAL-3.5MM-4; PARTNO OSTTE030104
JP7: POWER_JACKSLT; POWER_JACK_SLOT; PARTNO PJ-202A
JP8, JP9: M023.5MM; SCREWTERMINAL-3.5MM-2; PARTNO OSTTE020104
JP10: M03SCREW; SCREWTERMINAL-3.5MM-3; PARTNO OSTTE030104
JP11, JP12: M12NO_SILK; 1X12_NO_SILK
Q1, Q2: TRANSISTOR_NPNTO-92-AMMO; TO-92-AMMO; PARTNO PN2222ABU
R1, R2, R3, R4, R6: 1k; 1206; PARTNO ERJ-8ENF1001V
R5, R7, R8, R9: RESISTORKIT; AXIAL-0.3-KIT
RV1, RV2: 2k; 3362U; PARTNO 3362U-1-202LF
SJ1: SOLDERJUMPERNC; SJ_2S
SJ2: SOLDERJUMPERNO; SJ_2S-NO
STANDOFF1, STANDOFF2, STANDOFF3, STANDOFF4: STAND-OFF
U$1: PHOTON_SMD

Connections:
3.3V: JP1.2, JP2.2, JP12.12, SJ1.1, U$1.24 (3V3)
5V: C3.2, D1.A, IC1.3 (VCC), IC1.5 (VIO), JP3.2, JP4.2, JP5.2, JP7.PWR, JP10.2, SJ2.1
CANH: IC1.7 (CANH), JP8.2, JP9.2
CANL: IC1.6 (CANL), JP8.1, JP9.1
CANRX: IC1.4 (RXD), JP12.3, U$1.15 (D2)
CANTX: IC1.1 (TXD), JP12.2, U$1.14 (D1)
DETECTOR_1: JP11.2, R2.1, U$1.11 (A1)
DETECTOR_2: JP11.3, R4.1, U$1.10 (A2)
DETECTOR_SIG_1: C1.2, JP1.1, R2.2, RV1.P$2 (S)
DETECTOR_SIG_2: C2.2, JP2.1, R4.2, RV2.P$2 (S)
GND: C1.1, C2.1, C3.1, C4.2 (-), C5.2, IC1.2 (GND), IC1.8 (!STB), JP4.1, JP5.1, JP6.1, JP7.GND@1 (GNDBREAK), JP7.GND@2 (GND), JP11.11, JP12.9, Q1.1 (E), Q2.1 (E), R3.1, R5.P$1 (1), R7.P$1 (1), R8.P$1 (1), R9.P$1 (1), RV1.P$1 (E), RV2.P$1 (E), U$1.2 (GND), U$1.21 (GND)
INPUT_ENCODER_A: JP4.3, JP12.7, R7.P$2 (2), U$1.19 (D6)
INPUT_ENCODER_B: JP4.4, JP12.6, R5.P$2 (2), U$1.18 (D5)
LASER_EN: JP12.1, R1.1, U$1.13 (D0)
LASER_GND: JP1.4, JP2.4, Q1.3 (C)
LASER_VCC: JP1.3, JP2.3, SJ1.2, SJ2.2
MOTOR_KILL: D2.A, JP6.3, JP11.4, U$1.9 (A3)
MOTOR_SPEED: JP6.2, JP11.7, U$1.6 (DAC)
unnamed: Q1.2 (B), R1.2
unnamed: Q2.2 (B), R6.2
unnamed: D2.K (C), R3.2
unnamed: JP12.8, U$1.20 (D7)
unnamed: JP12.10, U$1.22 (VBAT)
unnamed: JP12.11, U$1.23 (!RST)
RX: JP11.9, U$1.4 (RX)
SERVO_1: JP3.3, JP11.5, U$1.8 (A4)
SERVO_2: JP10.3, JP11.6, U$1.7 (A5)
SERVO_EN: JP11.1, R6.1, U$1.12 (A0)
SERVO_GND: JP3.1, JP10.1, Q2.3 (C)
TX: JP11.10, U$1.3 (TX)
VIN: C4.1 (+), C5.1, D1.C, JP11.12, U$1.1 (VIN)
WHEEL_ENCODER_A: JP5.3, JP12.5, R9.P$2 (2), U$1.17 (D4)
WHEEL_ENCODER_B: JP5.4, JP12.4, R8.P$2 (2), U$1.16 (D3)
WKP: JP11.8, U$1.5 (WKP)

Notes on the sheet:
Ball detectors
Ball detector 1 3.5mm 4-pin terminal block
Ball detector 2 3.5mm 4-pin terminal block
CAN Bus
Encoders
Route CANH and CANL parallel to each other to the terminal block
Input crank encoder 3.5mm 4-pin terminal block
Ball wheel encoder 3.5mm 4-pin terminal block
Motor Control
To motor control board 3.5mm 3-pin terminal block
Power
2.1mm barrel jack center positive
Photon
Servos
3.5mm 3-pin terminal block
Mounting holes
3.5mm 2-pin terminal block

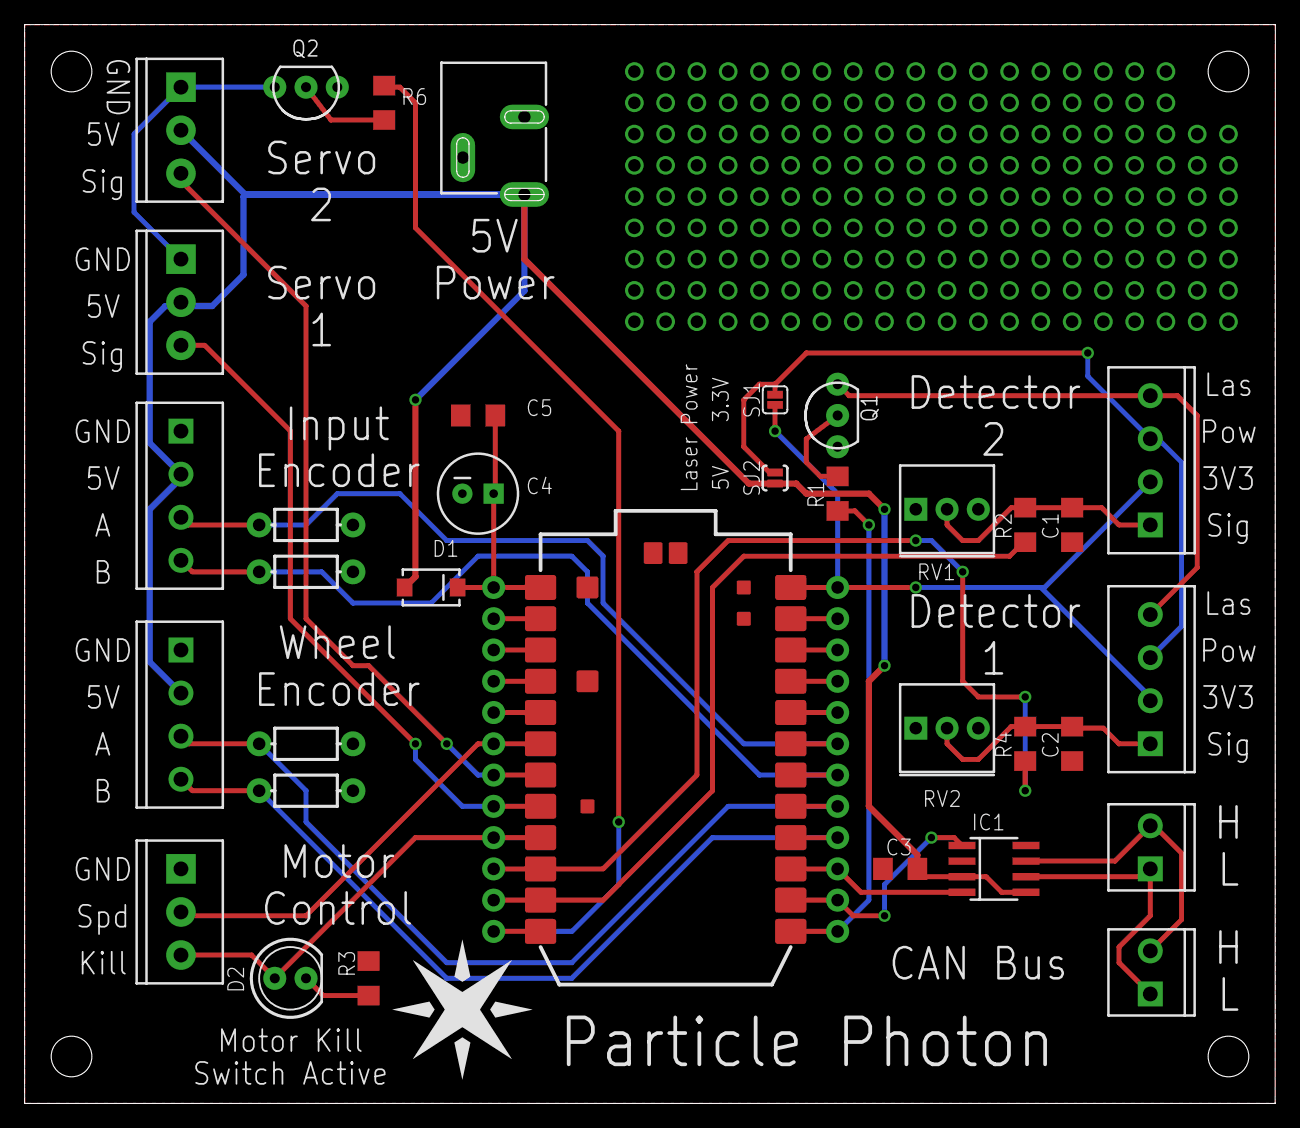
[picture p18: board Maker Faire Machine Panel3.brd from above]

Board: 2 copper layers, 101.6 x 87.6 mm, 40 parts (0 on the bottom side), 34 nets.

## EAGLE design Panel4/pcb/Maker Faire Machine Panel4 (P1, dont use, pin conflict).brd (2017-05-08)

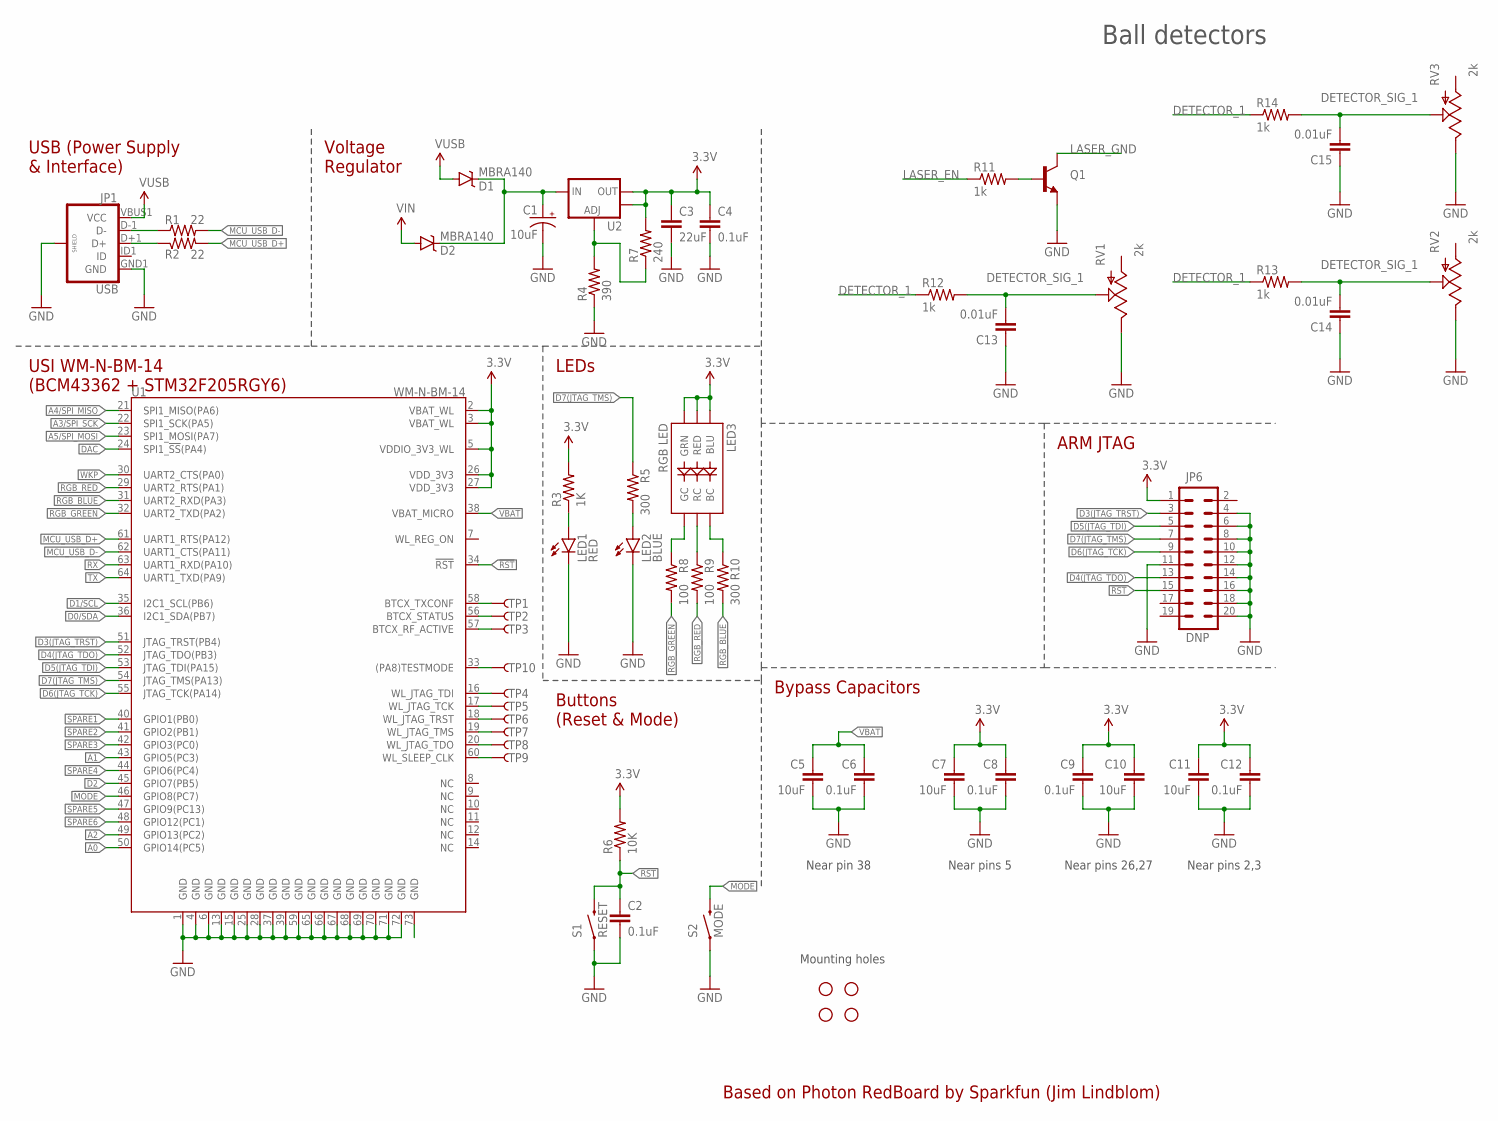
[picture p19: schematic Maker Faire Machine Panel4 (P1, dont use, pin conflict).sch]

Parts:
C1: 10uF; EIA3216
C2, C4, C6, C8, C9, C12: 0.1uF; 0603-CAP
C3: 22uF; 0805
C5, C7, C10, C11: 10uF; 0603-CAP
C13, C14, C15: 0.01uF; 1206; PARTNO 12065C103KAT2A
D1, D2: MBRA140; SMA-DIODE
JP1: USB; USB-B-MICRO-SMD_V03
JP6: DNP; 2X10
LED1: RED; LED-1206
LED2: BLUE; LED-1206
LED3: RGB LED; PLCC-6-LED
Q1: TRANSISTOR_NPNSOT89; SOT89; PARTNO PN2222ABU
R1, R2: 22; 0603-RES
R3: 1K; 0603-RES
R4: 390; 0603-RES
R5, R10: 300; 0603-RES
R6: 10K; 0603-RES
R7: 240; 0603-RES
R8, R9: 100; 0603-RES
R11, R12, R13, R14: 1k; 1206; PARTNO ERJ-8ENF1001V
RV1, RV2, RV3: 2k; 3362U; PARTNO 3362U-1-202LF
S1: RESET; TACTILE-PTH
S2: MODE; TACTILE-PTH
STANDOFF1, STANDOFF2, STANDOFF3, STANDOFF4: STAND-OFF
TP1, TP2, TP3, TP4, TP5, TP6, TP7, TP8, TP9, TP10: TEST-POINTTP_15TH_THRU; TP_15TH
U1: WM-N-BM-14
U2: V_REG_LM1117SOT223; SOT223

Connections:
3.3V: C3.1, C4.1, C7.1, C8.1, C9.1, C10.1, C11.1, C12.1, JP6.1, LED3.AB (BLU), LED3.AG (GRN), LED3.AR (RED), R3.2, R6.2, R7.2, U1.2 (VBAT_WL), U1.3 (VBAT_WL), U1.5 (VDDIO_3V3_WL), U1.26 (VDD_3V3), U1.27 (VDD_3V3), U2.2 (OUT), U2.4 (OUT)
!MODE: S2.3 (2), U1.46 (GPIO8(PC7))
!RST: C2.1, JP6.15, R6.1, S1.3 (2), U1.34 (!RST!)
A0: U1.50 (GPIO14(PC5))
A1: U1.43 (GPIO5(PC3))
A2: U1.49 (GPIO13(PC2))
A3/SPI_SCK: U1.22 (SPI1_SCK(PA5))
A4/SPI_MISO: U1.21 (SPI1_MISO(PA6))
A5/SPI_MOSI: U1.23 (SPI1_MOSI(PA7))
BTCX_RF_ACTIVE: TP3.P$1, U1.57 (BTCX_RF_ACTIVE)
BTCX_STATUS: TP2.P$1, U1.56 (BTCX_STATUS)
BTCX_TXCONF: TP1.P$1, U1.58 (BTCX_TXCONF)
D0/SDA: U1.36 (I2C1_SDA(PB7))
D1/SCL: U1.35 (I2C1_SCL(PB6))
D2: U1.45 (GPIO7(PB5))
D3(JTAG_TRST): JP6.3, U1.51 (JTAG_TRST(PB4))
D4(JTAG_TDO): JP6.13, U1.52 (JTAG_TDO(PB3))
D5(JTAG_TDI): JP6.5, U1.53 (JTAG_TDI(PA15))
D6(JTAG_TCK): JP6.9, U1.55 (JTAG_TCK(PA14))
D7(JTAG_TMS): JP6.7, R5.1, U1.54 (JTAG_TMS(PA13))
D+: JP1.D+1 (D+), R2.1
D-: JP1.D-1 (D-), R1.1
DAC: U1.24 (SPI1_!SS!(PA4))
DETECTOR_1: R12.1, R13.1, R14.1
DETECTOR_SIG_1: C13.2, C14.2, C15.2, R12.2, R13.2, R14.2, RV1.P$2 (S), RV2.P$2 (S), RV3.P$2 (S)
GND: C1.C (-), C2.2, C3.2, C4.2, C5.2, C6.2, C7.2, C8.2, C9.2, C10.2, C11.2, C12.2, C13.1, C14.1, C15.1, JP1.GND1 (GND), JP1.SHIELD1 (SHIELD), JP1.SHIELD2 (SHIELD), JP1.SHIELD3 (SHIELD), JP6.4, JP6.6, JP6.8, JP6.10, JP6.11, JP6.12, JP6.14, JP6.16, JP6.18, JP6.20, LED1.C, LED2.C, Q1.3 (E), R4.1, RV1.P$1 (E), RV2.P$1 (E), RV3.P$1 (E), S1.1, S2.1, U1.1 (GND), U1.4 (GND), U1.6 (GND), U1.13 (GND), U1.15 (GND), U1.25 (GND), U1.28 (GND), U1.37 (GND), U1.39 (GND), U1.59 (GND), U1.65 (GND), U1.66 (GND), U1.67 (GND), U1.68 (GND), U1.69 (GND), U1.70 (GND), U1.71 (GND), U1.72 (GND)
LASER_EN: R11.1
LASER_GND: Q1.2 (C)
MCU_USB_D+: R2.2, U1.61 (UART1_RTS(PA12))
MCU_USB_D-: R1.2, U1.62 (UART1_CTS(PA11))
unnamed: TP10.P$1, U1.33 ((PA8)TESTMODE)
unnamed: LED3.CG (GC), R8.1
unnamed: LED3.CR (RC), R9.1
unnamed: LED3.CB (BC), R10.1
unnamed: LED1.A, R3.1
unnamed: LED2.A, R5.2
unnamed: Q1.1 (B), R11.2
unnamed: C1.A (+), D1.C, D2.C, U2.3 (IN)
unnamed: R4.2, R7.1, U2.1 (ADJ)
RGB_BLUE: R10.2, U1.31 (UART2_RXD(PA3))
RGB_GREEN: R8.2, U1.32 (UART2_TXD(PA2))
RGB_RED: R9.2, U1.29 (UART2_RTS(PA1))
RX: U1.63 (UART1_RXD(PA10))
SPARE1: U1.40 (GPIO1(PB0))
SPARE2: U1.41 (GPIO2(PB1))
SPARE3: U1.42 (GPIO3(PC0))
SPARE4: U1.44 (GPIO6(PC4))
SPARE5: U1.47 (GPIO9(PC13))
SPARE6: U1.48 (GPIO12(PC1))
TX: U1.64 (UART1_TXD(PA9))
VBAT: C5.1, C6.1, U1.38 (VBAT_MICRO)
VIN: D2.A
VUSB: D1.A, JP1.VBUS1 (VCC)
WKP: U1.30 (UART2_CTS(PA0))
WL_JTAG_TCK: TP5.P$1, U1.17 (WL_JTAG_TCK)
WL_JTAG_TDI: TP4.P$1, U1.16 (WL_JTAG_TDI)
WL_JTAG_TDO: TP8.P$1, U1.20 (WL_JTAG_TDO)
WL_JTAG_TMS: TP7.P$1, U1.19 (WL_JTAG_TMS)
WL_JTAG_TRST: TP6.P$1, U1.18 (WL_JTAG_TRST)
WL_SLEEP_CLK: TP9.P$1, U1.60 (WL_SLEEP_CLK)

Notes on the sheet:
Near pin 38
Near pins 26,27
Near pins 5
Near pins 2,3
Voltage Regulator
USB (Power Supply & Interface)
ARM JTAG
Bypass Capacitors
LEDs
Buttons (Reset & Mode)
USI WM-N-BM-14 (BCM43362 + STM32F205RGY6)
Based on Photon RedBoard by Sparkfun (Jim Lindblom)
Mounting holes
Ball detectors

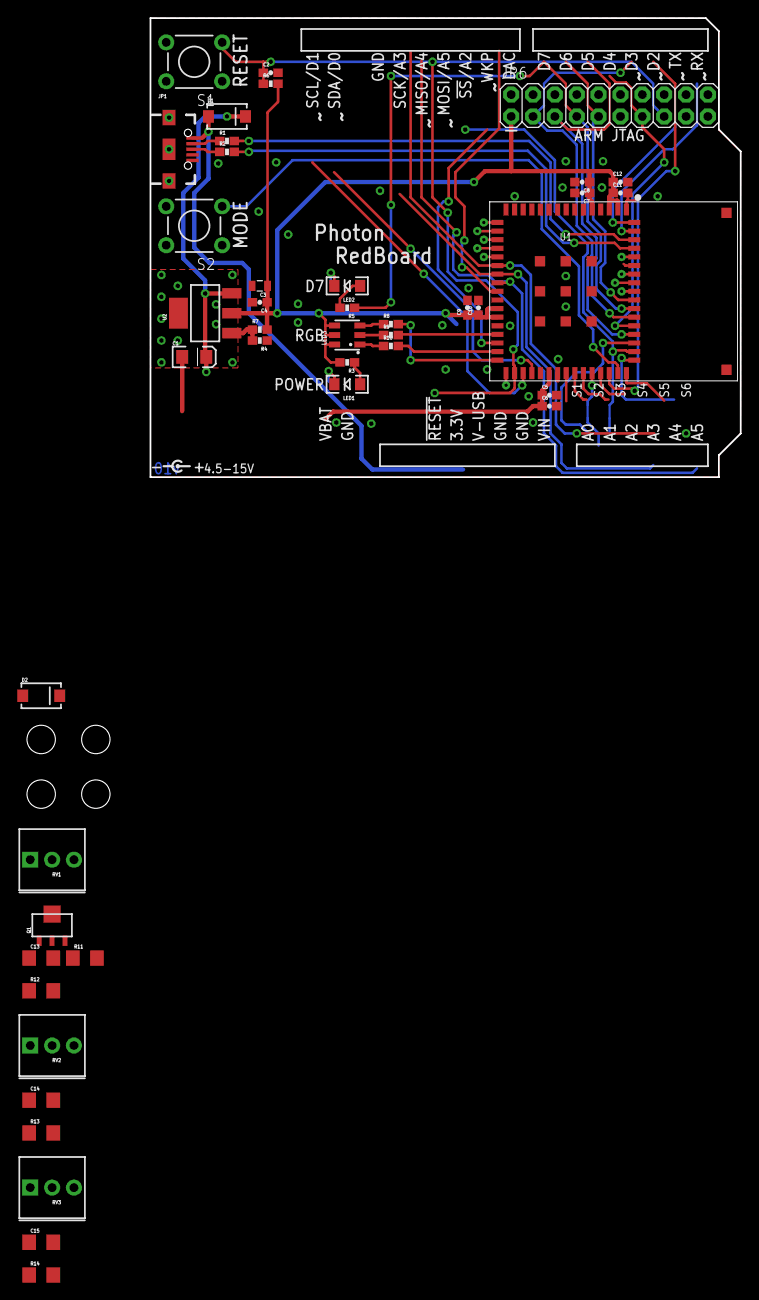
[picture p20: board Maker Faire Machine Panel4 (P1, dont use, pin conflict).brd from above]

Board: 2 copper layers, 68.6 x 53.3 mm, 58 parts (1 on the bottom side), 38 nets.

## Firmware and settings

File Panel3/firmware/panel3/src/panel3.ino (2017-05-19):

/*
 * Panel 3: Rotary encoder and ball wheel
 * 
 */

#include "mf2017-can.h"
#include "simple-storage.h"
#include "Encoder.h"
#include "beam-detector.h"

SYSTEM_THREAD(ENABLED);

/* Define AUTO_START to true during testing and false during the event.
 * It decides whether to wait for the MachineStart flag to turn on the
 * mechanisms or auto-start everything at boot.
 */
const bool AUTO_START = true;

// The main flag to enable or disable mechanisms
bool runMachine = AUTO_START;

/*
 * Pin usage:
 */

const auto LASER_ENABLE_PIN = D0;
const auto CAN_BUS_PINS = CAN_D1_D2;
const auto BALL_WHEEL_ENCODER_B_PIN = D3;
const auto BALL_WHEEL_ENCODER_A_PIN = D4;
const auto INPUT_CRANK_ENCODER_B_PIN = D5;
const auto INPUT_CRANK_ENCODER_A_PIN = D6;
const auto SERVO_ENABLE_PIN = A0;
const auto BALL_DETECTOR_2_PIN = A1;
const auto BALL_DETECTOR_1_PIN = A2;
const auto BALL_WHEEL_KILL_SWITCH_PIN = A3;
const auto SERVO_1_PIN = A4;
const auto SERVO_2_PIN = A5;
const auto BALL_WHEEL_MOTOR_SPEED_PIN = DAC;
const auto BALL_DETECTOR_3_PIN = WKP;
const auto WHEEL_TURN_PIN = TX;

/*
 * CAN communication
 */
BuiltinCAN can(CAN_BUS_PINS);
Communication comms(can);

/*
 * Input crank encoder
 */
Encoder inputEncoder(INPUT_CRANK_ENCODER_A_PIN, INPUT_CRANK_ENCODER_B_PIN);

/*
 * Ball wheel encoder
 */
Encoder wheelEncoder(BALL_WHEEL_ENCODER_A_PIN, BALL_WHEEL_ENCODER_B_PIN);

/*
 * Ball detectors
 */
BeamDetector detector1(BALL_DETECTOR_1_PIN, LASER_ENABLE_PIN);
BeamDetector detector2(BALL_DETECTOR_2_PIN, LASER_ENABLE_PIN);
BeamDetector detector3(BALL_DETECTOR_3_PIN, LASER_ENABLE_PIN);

/*
 * Servos
 */

Servo servo1;
Servo servo2;

/*
 * Config stored in EEPROM
 */
struct Config {
  uint32_t app;
  uint32_t ballCount1;
  uint32_t ballCount2;
  uint32_t ballCount3;
  uint16_t inputCrankPulsesPerRevolution;
  uint16_t inputCrankInterval;
  float ballWheelSpeedFactor;
  uint16_t ballWheelMinSpeed;
  uint16_t ballWheelMaxSpeed;
  uint8_t ballWheelStallDetection;
  uint8_t autoDoors;
  float wheelPulsesPerBall;
  uint8_t servo1OpenPos;
  uint8_t servo1ClosedPos;
  uint8_t servo2OpenPos;
  uint8_t servo2ClosedPos;
  uint16_t overrideSpeed;
} config;

Config defaultConfig = {
  /* app */ APP_CODE('M', 'F', '3', 7), // increment last digit to reset EEPROM on boot
  /* ballCount1 */ 0,
  /* ballCount2 */ 0,
  /* ballCount3 */ 0,
  /* inputCrankPulsesPerRevolution */ 1200,
  /* inputCrankInterval */ 100,
  /* ballWheelSpeedFactor */ 2000.0,
  /* ballWheelMinSpeed */ 200,
  /* ballWheelMaxSpeed */ 4000,
  /* ballWheelStallDetection */ 0,
  /* autoDoors */ 1,
  /* wheelPulsesPerBall */ 2400 / 36.0,
  /* servo1OpenPos */ 76,
  /* servo1ClosedPos */ 98,
  /* servo2OpenPos */ 65,
  /* servo2ClosedPos */ 87,
  /* overrideSpeed */ 2000,
};

Storage<Config> storage(defaultConfig);

/*
 * SETUP
 */

void setup() {
  Serial.begin();
  loadStorage();
  setupComms();
  setupDetectors();
  setupMotor();
  setupServos();
}

/*
 * LOOP
 */

void loop() {
  receiveComms();
  registerCloud();
  updateDetectors();
  readInputCrank();
  controlMotor();
  controlServos();
  printStatus();
  transmitComms();
  storeBallCount();
}

/*
 * Beam detectors
 */

bool beamBroken1 = false;
bool beamBroken2 = false;
bool beamBroken3 = false;
uint32_t ballCount1 = 0;
uint32_t ballCount2 = 0;
uint32_t ballCount3 = 0;

void setupDetectors() {
  detector1.begin(BeamDetector::POWER_OFF);
  detector2.begin(BeamDetector::POWER_OFF);
  detector3.begin(BeamDetector::POWER_OFF);

  // restore ballCounts from storage
  ballCount1 = config.ballCount1;
  ballCount2 = config.ballCount2;
  ballCount3 = config.ballCount3;
}

void updateDetectors() {
  detector1.enable(runMachine);
  detector2.enable(runMachine);
  detector3.enable(runMachine);

  beamBroken1 = detector1.beamBroken();
  beamBroken2 = detector2.beamBroken();
  beamBroken3 = detector3.beamBroken();

  // Count balls
  static uint32_t oldDetectionCount1 = 0;
  uint32_t detectionCount1 = detector1.detectionCount();
  if (detectionCount1 != oldDetectionCount1) {
    ballCount1 += detectionCount1 - oldDetectionCount1;
  }
  oldDetectionCount1 = detectionCount1;

  static uint32_t oldDetectionCount2 = 0;
  uint32_t detectionCount2 = detector2.detectionCount();
  if (detectionCount2 != oldDetectionCount2) {
    ballCount2 += detectionCount2 - oldDetectionCount2;
  }
  oldDetectionCount2 = detectionCount2;

  static uint32_t oldDetectionCount3 = 0;
  uint32_t detectionCount3 = detector3.detectionCount();
  if (detectionCount3 != oldDetectionCount3) {
    ballCount3 += detectionCount3 - oldDetectionCount3;
  }
  oldDetectionCount3 = detectionCount3;
}

/*
 * Input crank
 */

uint32_t inputCrankLastUpdate = 0;
long inputCrankPosition = 0;
long lastInputCrankPosition = 0;
float inputCrankSpeed = 0;
float inputCrankFactor = 0;

void readInputCrank() {
  // // FIXME: input bypassed to serial
  // if (Serial.available()) {
  //   char c = Serial.read();
  //   if (c >= '0' && c <= '9') {
  //     inputCrankSpeed = (c - '0') * 0.66;
  //   }
  // }
  // return;

  auto now = millis();
  if (now - inputCrankLastUpdate < config.inputCrankInterval) {
    return;
  }
  inputCrankLastUpdate = now;

  inputCrankPosition = inputEncoder.read();
  long deltaPosition = inputCrankPosition - lastInputCrankPosition;
  lastInputCrankPosition = inputCrankPosition;

  /* Convert pulses since the last interval to speed
   * speed_revolution_per_second = (pulses / pulses_per_revolution) / interval_ms * 1000 * ms_per_second
   */
  if (inputCrankFactor == 0) {
    // cache inputCrankFactor since it doesn't change often
    updateInputCrankFactor();
  }
  if (deltaPosition > 0) {
    inputCrankSpeed = deltaPosition * inputCrankFactor;
  } else {
    inputCrankSpeed = 0;
  }
  //Serial.printlnf("pos=%d delta=%d speed=%f", position, deltaPosition, inputCrankSpeed);
}

void updateInputCrankFactor() {
  inputCrankFactor = 1000.0 / (config.inputCrankPulsesPerRevolution * config.inputCrankInterval);
}

/*
 * Motor control
 */

const auto MOTOR_RUN = HIGH;
const auto MOTOR_KILL = LOW;

auto motorState = AUTO_START ? MOTOR_RUN : MOTOR_KILL;
uint32_t motorSpeed = 0;

uint32_t motorControlLastUpdate = 0;
const auto motorControlInterval = 100;
const auto motorStallMaxTime = 1000;
long wheelPosition = 0;
long oldWheelPosition = 0;
uint16_t motorStallCounter = 0;

bool wheelTurnOverride = false;
const auto WHEEL_TURN_PRESSED = LOW;

void setupMotor() {
  pinMode(BALL_WHEEL_KILL_SWITCH_PIN, OUTPUT);
  digitalWrite(BALL_WHEEL_KILL_SWITCH_PIN, MOTOR_KILL);
  pinMode(BALL_WHEEL_MOTOR_SPEED_PIN, OUTPUT);
  pinMode(WHEEL_TURN_PIN, INPUT_PULLUP);
}

void controlMotor() {
  auto now = millis();
  if (now - motorControlLastUpdate < motorControlInterval) {
    return;
  }
  motorControlLastUpdate = now;

  wheelTurnOverride = digitalRead(WHEEL_TURN_PIN) == WHEEL_TURN_PRESSED;

  // Scale input crank speed to a voltage in the 0-3.3V range to send to
  // the motor controller
  uint16_t maxSpeed = min(config.ballWheelMaxSpeed, 4095);
  motorSpeed = (uint32_t)(inputCrankSpeed * config.ballWheelSpeedFactor) + config.ballWheelMinSpeed;

  if (motorSpeed > maxSpeed) {
    motorSpeed = maxSpeed;
  }

  wheelPosition = wheelEncoder.read();

  // Safety setting of the motor
  // if the desired motor speed > 0 and there were no pulses on the encoder for 1 second,
  // trigger the motor controller kill switch until the machine start button is pressed again
  if (config.ballWheelStallDetection && inputCrankSpeed > 0) {
    if (wheelPosition == oldWheelPosition) {
      motorStallCounter++;
    }
  } else {
    motorStallCounter = 0;
  }

  // Stop the motor when the machine stop button is pressed
  // Start the motor when the machine start button is pressed
  // Stop the motor when the motor is powered but not moving
  if (!runMachine) {
    motorState = MOTOR_KILL;
  } else if (comms.MachineStart) {
    motorState = MOTOR_RUN;
  } else if (motorStallCounter > motorStallMaxTime / motorControlInterval) {
    motorState = MOTOR_KILL;
  }

  oldWheelPosition = wheelPosition;

  if (wheelTurnOverride) {
    motorSpeed = config.overrideSpeed;
    digitalWrite(BALL_WHEEL_KILL_SWITCH_PIN, MOTOR_RUN);
    analogWrite(BALL_WHEEL_MOTOR_SPEED_PIN, motorSpeed);
  } else {
    digitalWrite(BALL_WHEEL_KILL_SWITCH_PIN, motorState);
    analogWrite(BALL_WHEEL_MOTOR_SPEED_PIN, runMachine ? motorSpeed : 0);
  }
}

/*
 * Servos
 */

const auto SERVO_RUN = HIGH;
const auto SERVO_KILL = LOW;

uint8_t servo1Pos = 0;
uint8_t servo2Pos = 0;

uint32_t servoControlLastUpdate = 0;
const auto servoControlInterval = 100;

uint32_t servoActuations = 0;
uint32_t lastServoActuations = 0;

enum DoorState_e {
  DOORS_CLOSED,
  DOOR1_OPEN,
  DOOR2_OPEN,
  DOOR_STATE_MAX
} doorState = DOORS_CLOSED;

void setupServos() {
  servo1.attach(SERVO_1_PIN);
  servo2.attach(SERVO_2_PIN);
  pinMode(SERVO_ENABLE_PIN, OUTPUT);
  digitalWrite(SERVO_ENABLE_PIN, SERVO_KILL);
}

void controlServos() {
  auto now = millis();
  if (now - servoControlLastUpdate < servoControlInterval) {
    return;
  }
  servoControlLastUpdate = now;

  if (config.autoDoors) {
    // Change the servo position for every ball by counting the number of
    // pulses on the ball wheel
    servoActuations = (uint32_t)(wheelPosition / config.wheelPulsesPerBall);
    if (servoActuations != lastServoActuations) {
      // Pick a new door
      doorState = (DoorState_e)(random(DOOR_STATE_MAX));
    }
    lastServoActuations = servoActuations;
  }

  switch (doorState) {
    case DOOR1_OPEN:
      servo1Pos = config.servo1OpenPos;
      servo2Pos = config.servo2ClosedPos;
      break;
    case DOOR2_OPEN:
      servo1Pos = config.servo1ClosedPos;
      servo2Pos = config.servo2OpenPos;
      break;
    default:
      servo1Pos = config.servo1ClosedPos;
      servo2Pos = config.servo2ClosedPos;
      break;
  }

  servo1.write(servo1Pos);
  servo2.write(servo2Pos);
  digitalWrite(SERVO_ENABLE_PIN, runMachine ? SERVO_RUN : SERVO_KILL);
}

/*
 * CAN communication
 */

void setupComms() {
  comms.begin();
}

void receiveComms() {
  comms.receive();
  if (comms.MachineStop) {
    runMachine = false;
  } else if (comms.MachineStart) {
    runMachine = true;
  }
}

void transmitComms() {
  comms.Input3Active = (inputCrankSpeed > 0);
  comms.InputCrankSpeed = inputCrankSpeed;

  comms.BallCount3 = ballCount1 + ballCount2 + ballCount3;
  comms.IntegrationCountA = ballCount1;
  comms.IntegrationCountB = ballCount2;
  comms.IntegrationCountC = ballCount3;

  comms.transmit(MachineModules::Panel3);
}

/*
 * Debug printing
 */

uint32_t printLastUpdate = 0;
const auto printInterval = 100;

void printStatus() {
  auto now = millis();
  if (now - printLastUpdate < printInterval) {
    return;
  }
  printLastUpdate = now;

  Serial.printlnf(
    "%s crank=%d speed=%f wheel=%d motor=%d/%d stall=%d override=%d door=%d/%d/%d beams=%d/%d/%d balls=%d/%d/%d",
    runMachine ? "RUN " : "KILL ",
    inputCrankPosition,
    inputCrankSpeed,
    wheelPosition,
    motorSpeed,
    motorState,
    motorStallCounter,
    doorState,
    servo1Pos,
    servo2Pos,
    beamBroken1,
    beamBroken2,
    beamBroken3,
    ballCount1,
    ballCount2,
    ballCount3
  );
}

/*
 * Cloud functionality
 */
void registerCloud() {
  static bool registered = false;
  if (!registered && Particle.connected()) {
    registered = true;
    Particle.function("set", setConfigFromCloud);
    Particle.function("door", changeDoorState);
  }
}

// Call Particle cloud function "set" with name=value to change a config value
int setConfigFromCloud(String arg) {
    int equalPos = arg.indexOf('=');
    if (equalPos < 0) {
        return -1;
    }
    String name = arg.substring(0, equalPos);
    String value = arg.substring(equalPos + 1);

    if (name.equals("ballCount1")) {
      config.ballCount1 = value.toInt();
      ballCount1 = config.ballCount1;
    } else if (name.equals("ballCount2")) {
      config.ballCount2 = value.toInt();
      ballCount2 = config.ballCount2;
    } else if (name.equals("ballCount3")) {
      config.ballCount3 = value.toInt();
      ballCount3 = config.ballCount3;
    } else if (name.equals("inputCrankPulsesPerRevolution")) {
      config.inputCrankPulsesPerRevolution = value.toInt();
      // recompute cached factor
      updateInputCrankFactor();
    } else if (name.equals("inputCrankInterval")) {
      config.inputCrankInterval = value.toInt();
      // recompute cached factor
      updateInputCrankFactor();
    } else if (name.equals("ballWheelSpeedFactor")) {
      config.ballWheelSpeedFactor = value.toFloat();
    } else if (name.equals("ballWheelMinSpeed")) {
      config.ballWheelMinSpeed = value.toInt();
    } else if (name.equals("ballWheelMaxSpeed")) {
      config.ballWheelMaxSpeed = value.toInt();
    } else if (name.equals("ballWheelStallDetection")) {
      config.ballWheelStallDetection = value.toInt();
    } else if (name.equals("autoDoors")) {
      config.autoDoors = value.toInt();
    } else if (name.equals("wheelPulsesPerBall")) {
      config.wheelPulsesPerBall = value.toFloat();
    } else if (name.equals("servo1OpenPos")) {
      config.servo1OpenPos = value.toInt();
    } else if (name.equals("servo1ClosedPos")) {
      config.servo1ClosedPos = value.toInt();
    } else if (name.equals("servo2OpenPos")) {
      config.servo2OpenPos = value.toInt();
    } else if (name.equals("servo2ClosedPos")) {
      config.servo2ClosedPos = value.toInt();
    } else if (name.equals("overrideSpeed")) {
      config.overrideSpeed = value.toInt();
    } else {
      return -2;
    }

    storage.store(config);
    return 0;
}

int changeDoorState(String arg) {
  doorState = (DoorState_e) arg.toInt();
  return 0;
}

/*
 * Persistent storage
 */

void loadStorage() {
  storage.load(config);
}

// Write ball count to EEPROM every N balls
void storeBallCount() {
  static const auto STORE_BALLS_DELTA = 20;
  if (ballCount1 - config.ballCount1 >= STORE_BALLS_DELTA) {
    config.ballCount1 = ballCount1;
    storage.store(config);
  }
  if (ballCount2 - config.ballCount2 >= STORE_BALLS_DELTA) {
    config.ballCount2 = ballCount2;
    storage.store(config);
  }
  if (ballCount3 - config.ballCount3 >= STORE_BALLS_DELTA) {
    config.ballCount3 = ballCount3;
    storage.store(config);
  }
}

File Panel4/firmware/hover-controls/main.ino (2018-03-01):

#include "Hover.h"


#include "can-lib/bitset.h"
#include "can-lib/can-interface.h"
#include "can-lib/mf2017-can.h"


#define STEP_CLOCK_DURATION 1

#define BUMP_BTN_PIN1 B0
#define BUMP_BTN_PIN2 B1

#define STEPPER_EN_PIN C0
#define STEPPER_DIRECTION_PIN C1
#define STEPPER_STEP_PIN D2

#define LASER_ENABLE A0
#define LASER_GATE1 A1
#define LASER_GATE2 A2
#define LASER_GATE3 A3

#define HOVER_TS_PIN D4
#define HOVER_RST_PIN D5

#define BALL_PUMP_PIN C3
#define BALLS_FULL_PIN C2

#define STEPPER_DIRECTION_LEFT LOW
#define STEPPER_DIRECTION_RIGHT HIGH

//
//  Motor Stuff
//

enum  MotorAction { STOP = 0, LEFT, RIGHT, END };
void controlMotor(MotorAction action);

MotorAction _myMotorAction = MotorAction::STOP;
bool volatile _isMotorStepping = false;
bool volatile _isBumpSwitchOn = false;
bool volatile _isLeftBumpSwitchOn = false;
bool volatile _isRightBumpSwitchOn = false;
bool volatile _stepState = false;

//Timer stepperTimer(1, stepperCallback);
Timer bumperChecker(50, bumperCallback);


//
//  Hover Stuff
//


#define GESTUREMODE 0x00    //0x00 = disable gestures, 0x01 = enable gestures
#define TOUCHMODE 0x00      //0x00 = disable touch, 0x01 = enable touch
#define TAPMODE 0x01        //0x00 = disable taps, 0x01 = enable taps, 0x02 = single taps only, 0x03 = double taps only
#define POSITIONMODE 0x01   //0x00 = disable position tracking, 0x01 = enable position tracking

Hover hover = Hover(HOVER_TS_PIN, HOVER_RST_PIN, GESTUREMODE, TOUCHMODE, TAPMODE, POSITIONMODE );

unsigned long lastHoverCommand = 0;
unsigned long lastHoverCheck = 0;
bool state = false;

// TODO: how long should this run for?
#define DISPENSE_BALL_DURATION 1250
bool dispensingBall = false;
unsigned long startedDispensingBallTime = 0;

SYSTEM_MODE(MANUAL);



//CANChannel can(CAN_C4_C5);
BuiltinCAN can(CAN_C4_C5);
Communication comms = Communication(can);
#define CAN_PRINT_MESSAGE_ID 0x204




// laser gate stuff
#define PRINT_DELAY 60000
int counters[4] = {0,0,0,0};
unsigned long lastPrintTime = 0;

bool isMachineStopped = false;
bool blink_state = false;

/*
    How to wire it up!

    Behaviors!

        move your hand left, the platform moves left
        right, right

        if you a stop switch, stop moving in that direction.

        if you touch the hover pad, release a ball


    TODOS;
        fire up the "ball pump pin when touched"
        fix the backoff / movement behavior Mohit added
        cleanup code a bit
*/


void setup() {
    Serial.begin(115200);
    hover.begin();

    pinMode(STEPPER_STEP_PIN, OUTPUT);
    pinMode(STEPPER_DIRECTION_PIN, OUTPUT);
    pinMode(STEPPER_EN_PIN, OUTPUT);

    pinMode(BUMP_BTN_PIN1, INPUT_PULLUP);
    pinMode(BUMP_BTN_PIN2, INPUT_PULLUP);

    pinMode(BALL_PUMP_PIN, OUTPUT);
    pinMode(BALLS_FULL_PIN, INPUT);


    pinMode(LASER_ENABLE, OUTPUT);
    digitalWrite(LASER_ENABLE, HIGH);

    pinMode(LASER_GATE1, INPUT);
    pinMode(LASER_GATE2, INPUT);
    pinMode(LASER_GATE3, INPUT);

    pinMode(D7, OUTPUT);

    //Initialize default states
    digitalWrite(STEPPER_EN_PIN, HIGH); //disable stepper motor driver
    analogWrite(STEPPER_STEP_PIN, 128, 1200);

    // run me forever
    bumperChecker.start();

    //start up the can bus
    //can.begin(500000);
    comms.begin();

    PMIC power;
    power.disableCharging();
}

void loop() {
    hoverTick();

    checkLaserGates();

    dispenseBallTick();

    transmitCANUpdates();

    if (isMachineStopped) {
        digitalWrite(D7, (blink_state) ? HIGH : LOW);
        blink_state = !blink_state;
        delay(10);
    }
}

unsigned long lastCanUpdateTime = 0;
#define CAN_UPDATE_FREQUENCY 250

void transmitCANUpdates() {
    comms.receive();

    unsigned long now = millis();
    if (( now - lastCanUpdateTime ) < CAN_UPDATE_FREQUENCY) {
        return;
    }
    lastCanUpdateTime = now;
    Serial.println("sending hero update...");



    if (comms.MachineStart) {
        isMachineStopped = false;
    }
    else if (comms.MachineStop) {
        isMachineStopped = true;
    }


    //case Panel4Status:

    comms.BallDropperLeftLimit = _isLeftBumpSwitchOn;//getBit(m.data, 0, 1);
    comms.BallDropperRightLimit = _isRightBumpSwitchOn;//getBit(m.data, 0, 2);

    // these are set by the print routines
    //    comms.PrintingPrizeA
    //    comms.PrintingPrizeB
    //    comms.PrintingPrizeC

    // these are set by the hover routines
    //    comms.HoverPositionLR = getU8(m.data, 2);
    //    comms.HoverPositionUD = getU8(m.data, 3);


    // what are these?
    //    comms.Reservoir4Status = static_cast<ReservoirStatus>(getU8(m.data, 1));
    //    comms.Input4Active = getBit(m.data, 0, 0);
    //    comms.BallCount4 = getU32(m.data, 4);


    //case Panel4OutputStatus:
    comms.PrizeCountA = counters[0];
    comms.PrizeCountB = counters[1];
    comms.PrizeCountC = counters[2];

    comms.transmit(MachineModules::Panel4);


    // reset momentary elements
    comms.PrintingPrizeA = false;
    comms.PrintingPrizeB = false;
    comms.PrintingPrizeC = false;
}


void checkLaserGates() {
    int buttonDownValue = LOW;

    bool buttonOne = digitalRead(LASER_GATE1) == buttonDownValue;
    bool buttonTwo = digitalRead(LASER_GATE2) == buttonDownValue;
    bool buttonThree = digitalRead(LASER_GATE3) == buttonDownValue;

    int imageNumber = -1;

    //
    //  Count the balls
    //

    if (buttonOne) {
        imageNumber = 5;
        counters[0]++;
        comms.PrintingPrizeA = true;
    }
    else if (buttonTwo) {
        imageNumber = 6;
        counters[1]++;
        comms.PrintingPrizeB = true;
    }
    else if (buttonThree) {
        imageNumber = 2;
        counters[2]++;
        comms.PrintingPrizeC = true;
    }

    //
    //  If enough time has passed (print the images)
    //

    unsigned long now = millis();
    if ((imageNumber >= 0) && ((now - lastPrintTime) > PRINT_DELAY)) {
        lastPrintTime = now;

        if (imageNumber >= 0) {
            Serial.println("1,2,3 " + String(buttonOne) + "," + String(buttonTwo) + "," + String(buttonThree));

            Serial.println("Printing image " + String(imageNumber));
            sendPrintCommand(imageNumber);
        }
    }
}


void hoverTick() {

    // read the hover interface
    hover.readI2CData();
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

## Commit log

2017-03-27 Prototype for Overview Display
2017-04-26 Remove duplicate encoder test firmware
2017-04-26 Update encoder interrupt to use direct memory access to pin
2017-04-29 add libraries
    [Circuit diagram.fzz]
2017-04-29 Add missing wire
2017-04-29 add detector assembled image
2017-04-29 add drill tip
2017-04-29 add detector bracket STL model
    [Ball Detector F.stl]
2017-04-29 add 3d printer settings
2017-05-01 Add Encoder library
    [Circuit diagram.fzz]
2017-05-04 Draft of schematic for panel 3
    [Circuit diagram.fzz, Maker Faire Machine Panel3.brd, Maker Faire Machine Panel3.sch]
2017-05-04 Add 2nd CAN terminal block for ease of wiring
    [Maker Faire Machine Panel3.brd, Maker Faire Machine Panel3.sch]
2017-05-04 Increase cutoff frequency of ball detector lowpass
    [Maker Faire Machine Panel3.brd, Maker Faire Machine Panel3.sch]
2017-05-04 Finished Panel 3 PCB Layout
    [Maker Faire Machine Panel3.brd, Maker Faire Machine Panel3.sch, Maker Faire Machine Panel3_BOM.csv]
2017-05-04 Add Gerbers
    [Maker Faire Machine Panel3.brd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]
2017-05-04 Update panel 3 PDF schematics
2017-05-05 Update Panel 3 PCB after Eric's comments
    [Maker Faire Machine Panel3.brd, Maker Faire Machine Panel3.sch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]
2017-05-07 Add CAN implementation for Raspberry Pi
2017-05-08 Fix LED orientation
    [Maker Faire Machine Panel3.brd, Maker Faire Machine Panel3.sch]
2017-05-08 Panel 4 PCB work in progress
    [Maker Faire Machine Panel4 (Electron).brd, Maker Faire Machine Panel4 (Electron).sch, Maker Faire Machine Panel4 (P1, dont use, pin conflict).brd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]
2017-05-08 First version of panel 4 PCB done
    [Maker Faire Machine Panel4 (Electron).brd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]
2017-05-09 Wired up Hero firmware to website to output JSON
2017-05-11 Add round ball detector
    [Round ball detector A.stl]
2017-05-11 Move holes in round ball detector
    [Round ball detector A.stl]
2017-05-11 Add round detector B
    [Round ball detector B.stl]
2017-05-11 Add DigiKey BOM for panel 4
    [Maker Faire Machine Panel4 (Electron)_OrderUploadDigiKey.csv]
2017-05-11 Fix typo in Lighting code
    [lighting.ino]
2017-05-11 Update firmware for panel 3
    [Maker Faire Machine Panel3.brd]
2017-05-13 adding printer firmware
2017-05-16 Update Panel 3 firmware
    [Maker Faire Machine Panel4 (Electron).brd]
2017-05-16 got the laser gates working enough for testing
2017-05-17 updating wiring notes, build scripts
2017-05-18 adding can bus tester
2017-05-18 adding laser gates / CAN print command
2017-05-18 adding can bus transmit / recieve / counters / libs
2017-05-18 Add button to turn wheel
2017-05-18 mostly working except CAN bus
2017-05-20 fixing ball pump hardware with software
    [panel2.ino]

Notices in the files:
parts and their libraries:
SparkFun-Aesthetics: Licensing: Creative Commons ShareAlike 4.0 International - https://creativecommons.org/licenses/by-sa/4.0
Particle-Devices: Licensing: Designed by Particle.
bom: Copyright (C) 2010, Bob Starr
